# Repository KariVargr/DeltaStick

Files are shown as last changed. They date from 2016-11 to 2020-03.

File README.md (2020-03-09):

# DeltaStick
Delta Parallel Robot/Kinematics base flight stick to replace a Throttle only unit for Space Flight Sims

# Update
This project Got put on hold almost in 2018 due to Work, Life and changes in how the same it was building built for changes. i will see about Exporting Editable STL in the near future, if they are still around.

Sorry for the long delay on getting this info up and useable for everyone, i had to change a few elements to make it easier for some one to built it with out taps

Parts List Delta Body

(9) 6-32 Machine Nuts
(9) 6-32 Machine Screws 1 1/2in
(3-9) 6-32 Machine Screws 3/8in

(24) 4-40 Machine Nuts
(24) 4-40 Machine Screws Flat Head 3/4in

(9) 5/16 Machine Nuts
(3) 5/16 3in Bolt
(6) 5/16 Lock Nuts
(6) 5/15 Washer (2644)
(3) Finishing Washer
Springs

(3) 13GA 100RPM geared motor 12V (Planning on testing the 60RPM)
http://leeselectronic.com/en/product/41502.html

(3) AS5600 Hall Effect
http://www.digikey.com/product-detail/en/ams/AS5600-ASOM/AS5600-ASOMCT-ND/4914333

SMT Breakout PCB for SOIC-8
https://www.adafruit.com/product/1212

(3) 100nf capacitors
(3) 1uf capacitors

Ardunio Leonardo or Pro Micro

12V 2A DC Power Supply.

(3) TA7291SG or L298N 
You will need to find something simalure. once i have time to find a replacment this will be udpated.
(Option to Replace this with L298N Motor Driver, 2 to 3 of these will work)

(3) 10K Resistors
(3) 1k Resistors
(3) 2N3904

Wire
Prototyping PCB

(12) 608ZZ Bearings

Joystick

(6) 6-32 Machine Nuts
(6) 6-32 Machine Screws 3/4in
(9) 6-32 Machine Screws 1 1/2in

(13) Tact
(18) 10K Resistors

On-Off-On Toggle Switch

MCP23017

Thumb Joystick
https://www.sparkfun.com/products/9032

Tools

3D Printer (or Order Prints from a online site)

Small File
Sand Paper

13MM (1/2in) Wrench/Socket
14MM (9/16) Wrench/Socket

Side Cutter.

AC / Crazy Glue

Sodering Iron
Soder

wire striper with screw cutter

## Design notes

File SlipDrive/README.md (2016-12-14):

# DeltaStick Slip Drive/Axle/Rod?

(6) 608ZZ Bearings
(12) 5/16 Machine Nuts
(3) 5/16 3in Bolt / ReadyRod (Will need to be treaded all the way to the end)
(6) 5/16 Lock Nuts
(6) 5/15 Washer (2644)
(3) Finishing Washer
Springs

Parts: Each build out will need
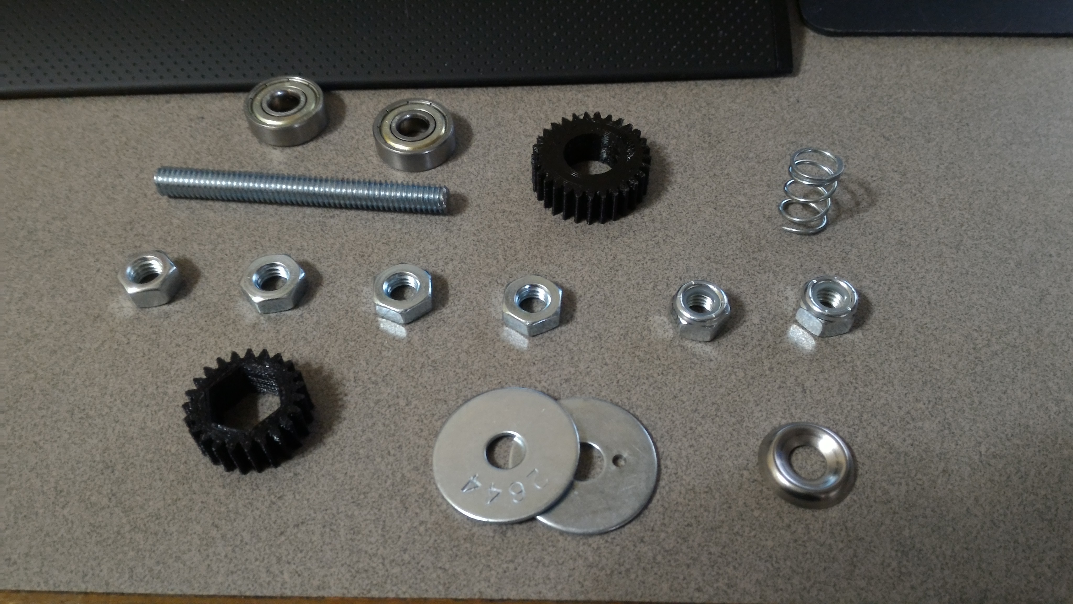
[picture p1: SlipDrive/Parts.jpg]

(2) 608ZZ Bearings
(1) 5/16 Bolt/Rod 
(4) 5/16 Machine Nuts
(2) 5/16 Lock Nuts
(2) 5/15 Washer (2644)
(1) Finishing Washer
and a Spring.

The Spring needs to fit over the 5/16 Rod with space to move, and can be cut to size but about 1in or less in length will work.

Step 1:
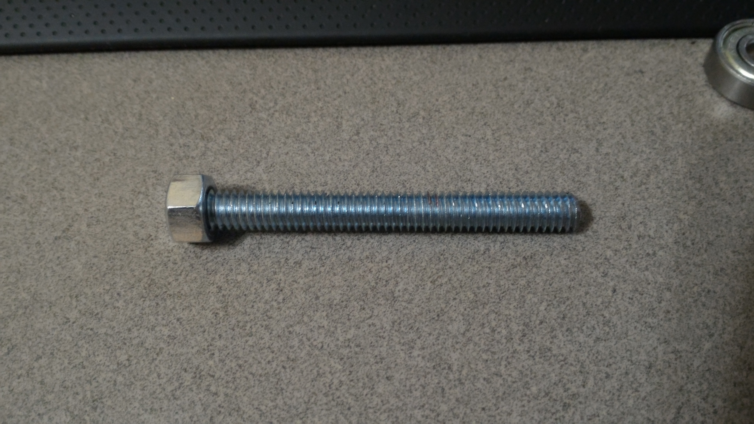
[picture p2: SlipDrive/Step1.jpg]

If you have a Bolt make sure it is threaded all they way to the end.
If you are using Ready Rod, or Threaded Rod Make sure its 3 In in length and place a 5/16 Machine Nuts at one end

Step 2:
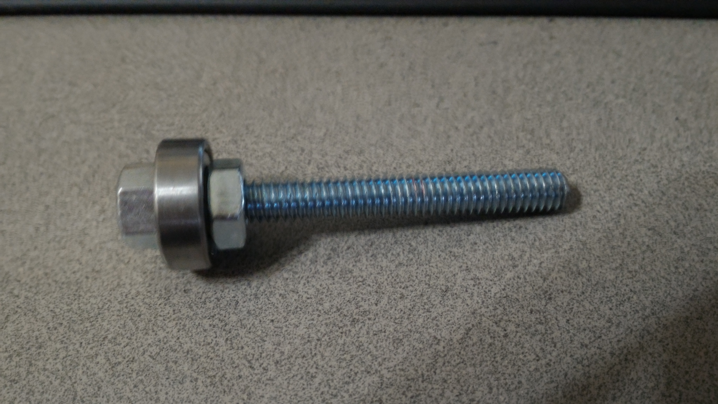
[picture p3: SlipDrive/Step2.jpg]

Slid on a 608ZZ Bearing Followed by a 5/16 Machine Nut

Step 3: 
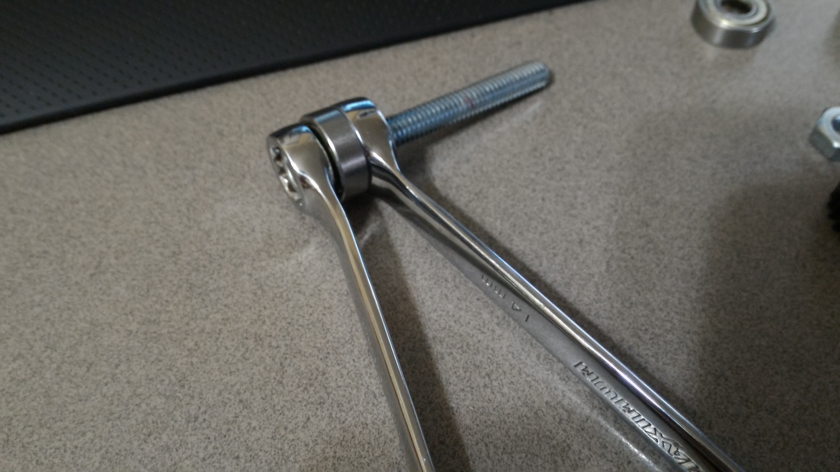
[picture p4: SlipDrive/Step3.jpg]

Tighten the 2 nuts against the bearing. the outside of the bearing should still move freely. 

Step 4: 
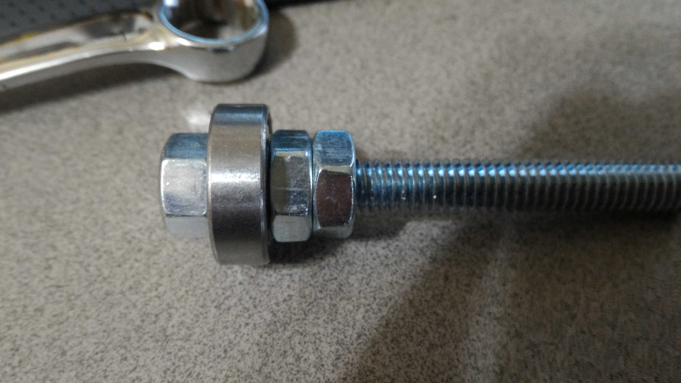
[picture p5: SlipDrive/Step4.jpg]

Place another 5/16 Machine Nut on. 

Step 5: 
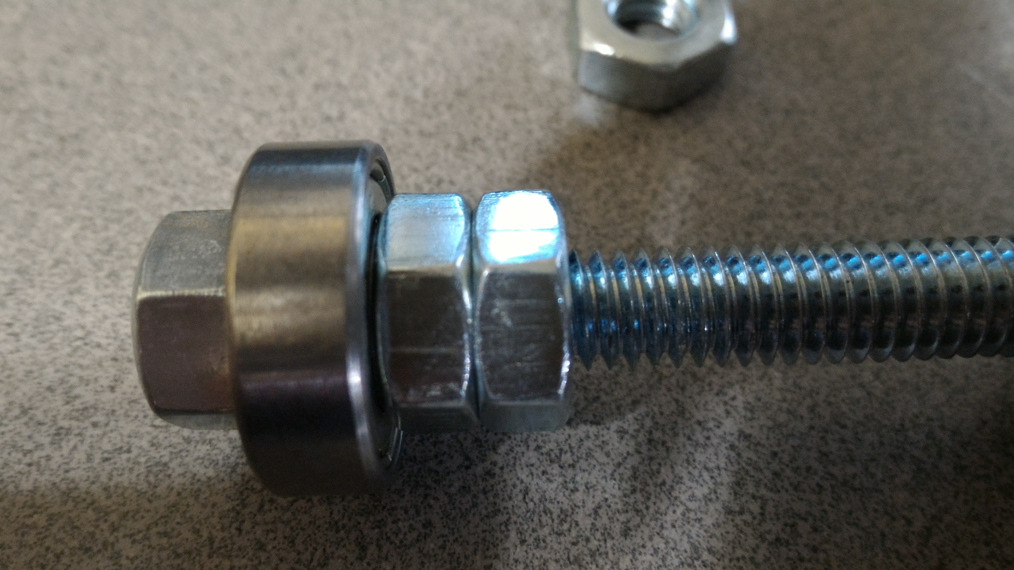
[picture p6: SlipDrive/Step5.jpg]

Tight the Nut down to the one next to it until they align in the picture.
If they cant be tightened to alignment try flipping the nut over or sanding one side of it to achieve the goal
None of the nuts should come off by hand at this point.

Step 6:
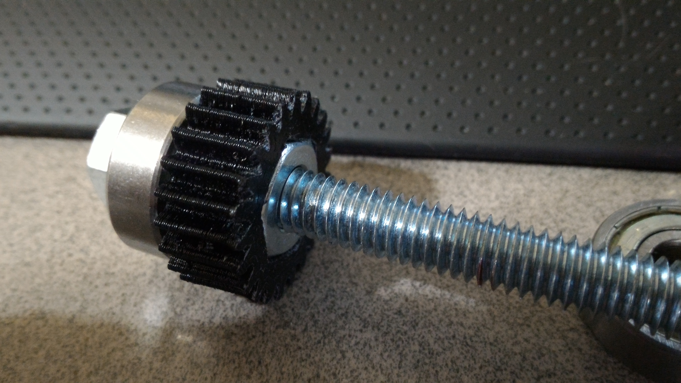
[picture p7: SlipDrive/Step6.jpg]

Slid the Printed Gear over the Machine Nuts, the gear should be centered between the nuts.

Step 7:
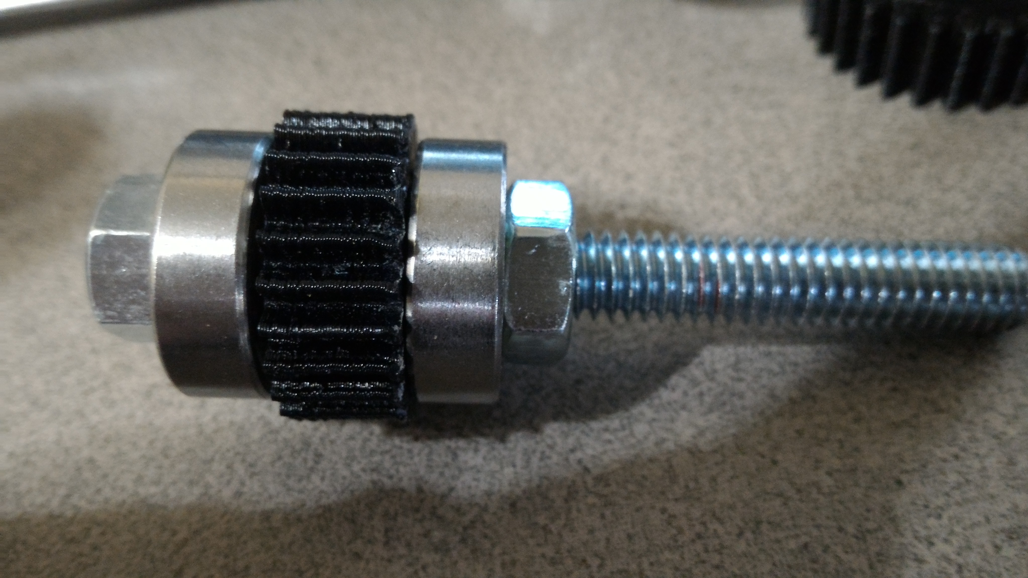
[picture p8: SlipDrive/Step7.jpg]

Slide a 2nd 608ZZ Bearing Followed by a 5/16 Machine Nut 
Tighten the nut against the bearing. the outside of the bearing should still move freely. 

No Show: At this point you would want to put the gearwall print on to the rod.

Step 8:
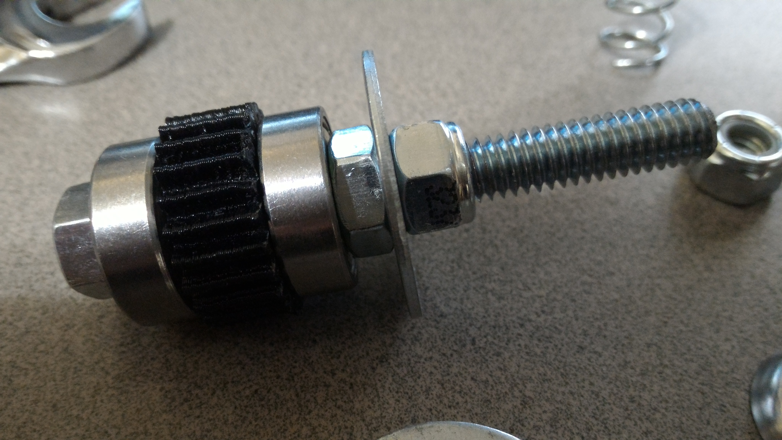
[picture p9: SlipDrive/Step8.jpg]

Slide a 5/15 Washer on followed by a 5/16 Lock Nut
Tighten the nut against the Washer.

Step 9:
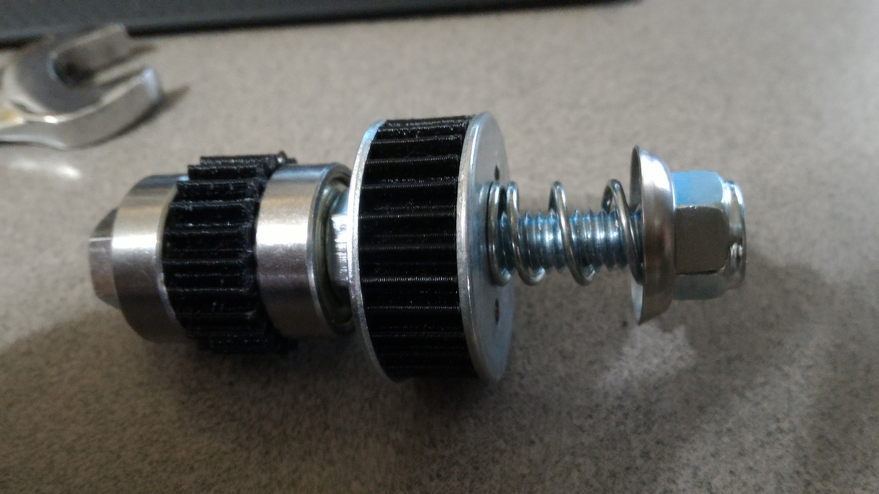
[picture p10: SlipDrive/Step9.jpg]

Place the 29T Slip Gear over the Lock Nut followed by a 5/15 Washer, Spring, Finishing Washer and Last 5/16 Lock Nut.
Tighten the nut down to a hold the stack together as in picture.

The Spring can be trimmed to allow max Slip when in the position pictured.
By Tightening the Lock Nut at the end the Friction will increase.

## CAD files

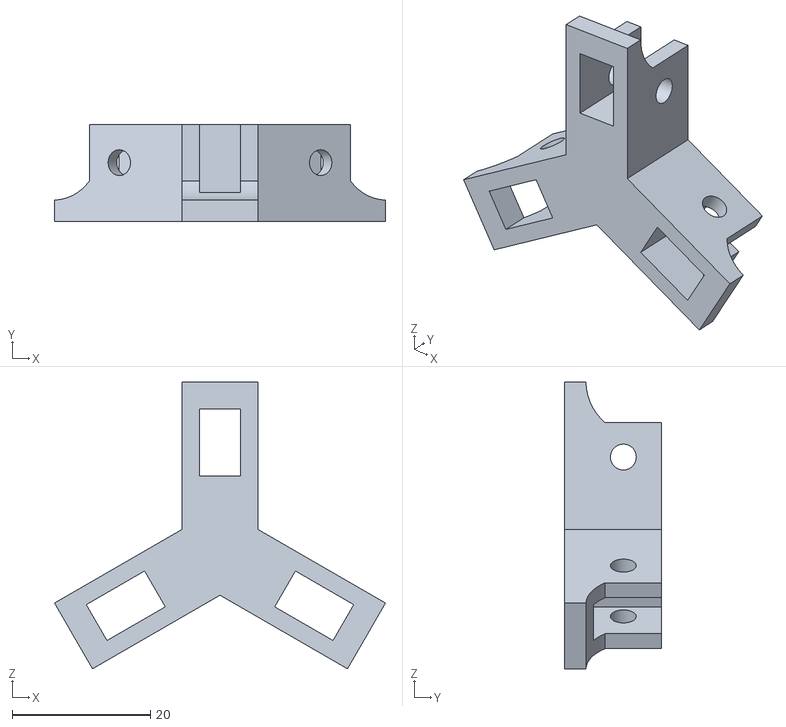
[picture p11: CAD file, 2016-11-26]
STL/CenterBot.stl
47.9 x 14.0 x 41.5

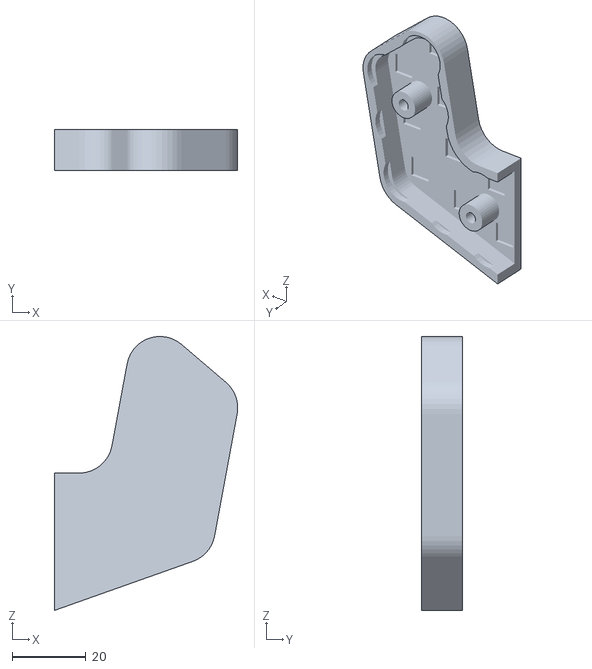
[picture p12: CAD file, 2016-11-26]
STL/JoyStick/CoverBack.STL
49.6 x 11.0 x 74.1

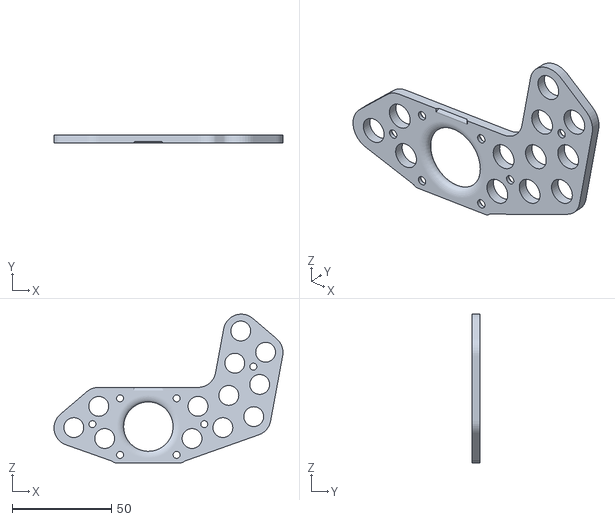
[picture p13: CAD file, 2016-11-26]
STL/JoyStick/Cover.STL
115.4 x 4.00 x 74.9

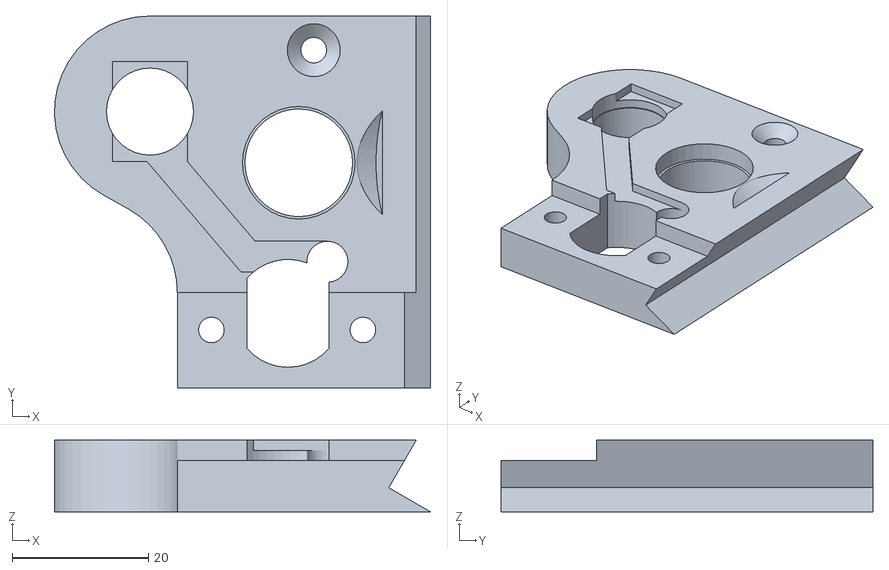
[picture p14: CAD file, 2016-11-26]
STL/MagWall.STL
55.1 x 54.5 x 10.5

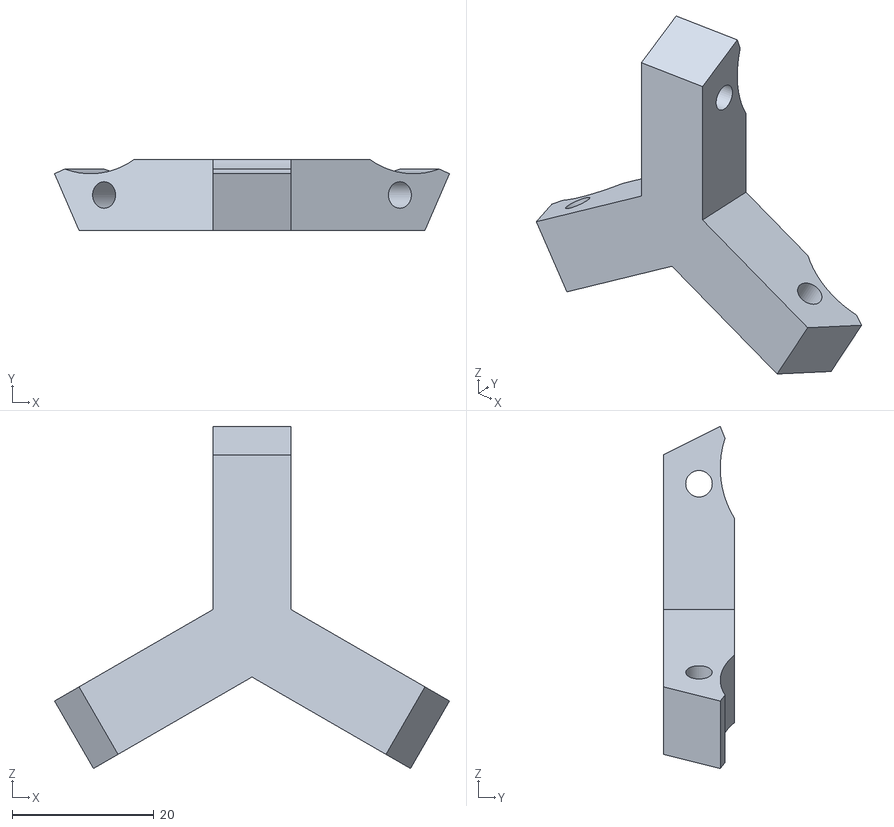
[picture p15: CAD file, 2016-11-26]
STL/CenterTop.STL
55.7 x 10.0 x 48.3

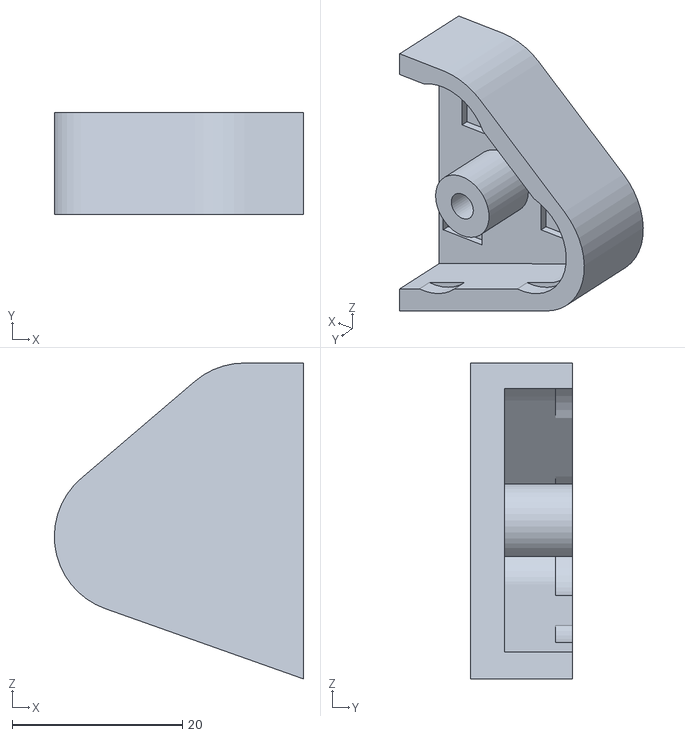
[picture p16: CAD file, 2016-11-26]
STL/JoyStick/CoverBackB.STL
29.3 x 12.0 x 37.2

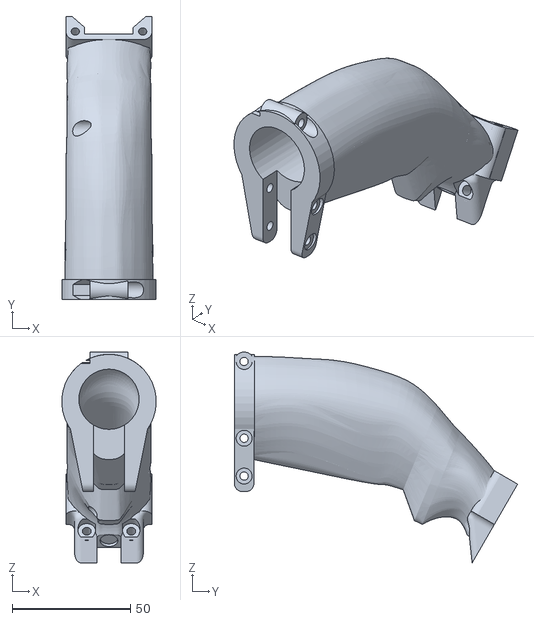
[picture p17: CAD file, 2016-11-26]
STL/JoyStick/BodyScaled.STL
39.9 x 119.9 x 89.3

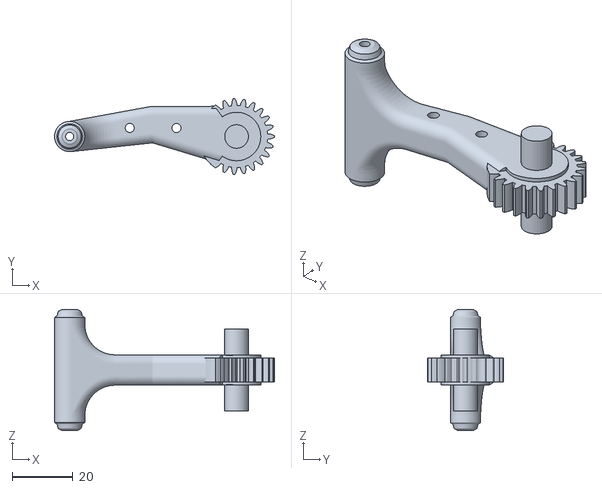
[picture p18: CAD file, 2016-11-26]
STL/LowerArmGearedCir.STL
72.5 x 25.0 x 40.0

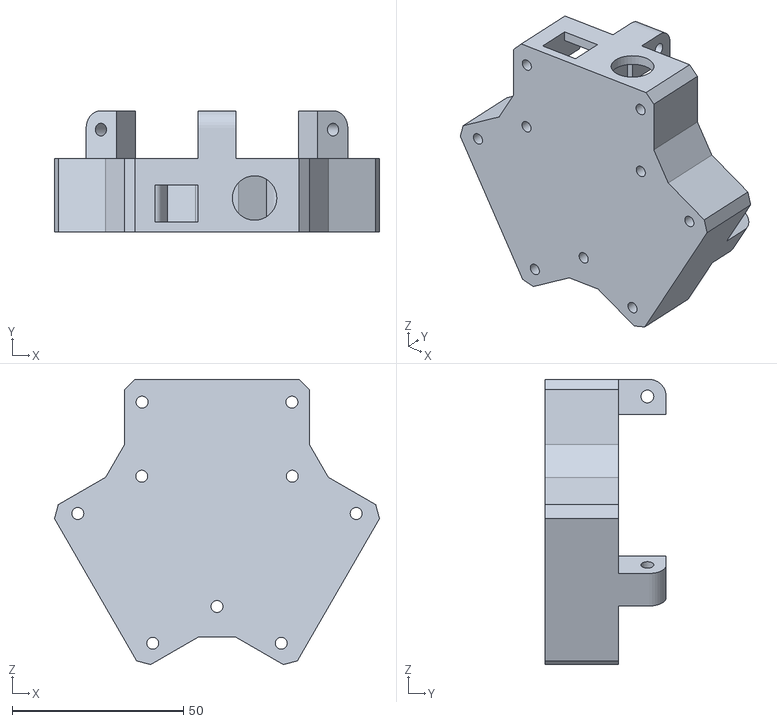
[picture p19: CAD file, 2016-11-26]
STL/ControlBox.STL
95.0 x 35.5 x 83.4

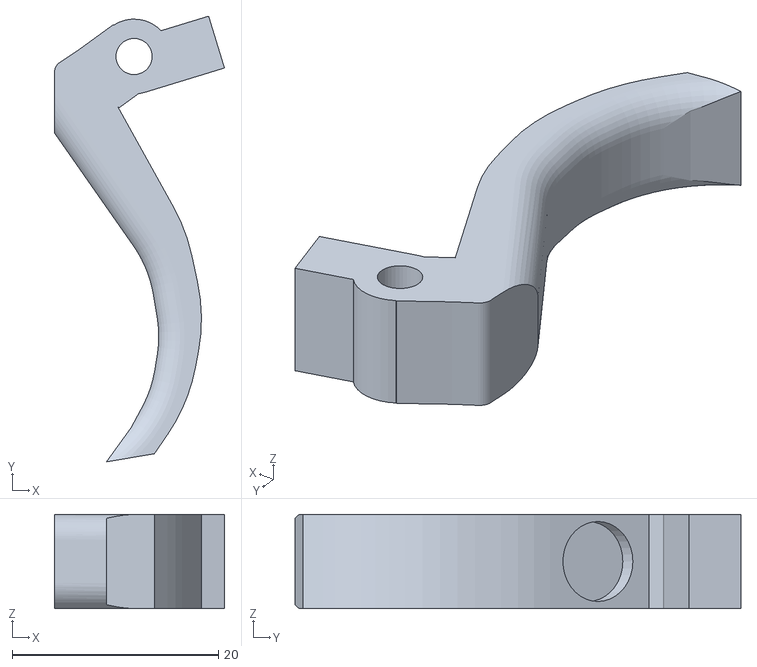
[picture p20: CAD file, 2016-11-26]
STL/JoyStick/Trigger.STL
16.5 x 43.2 x 9.12

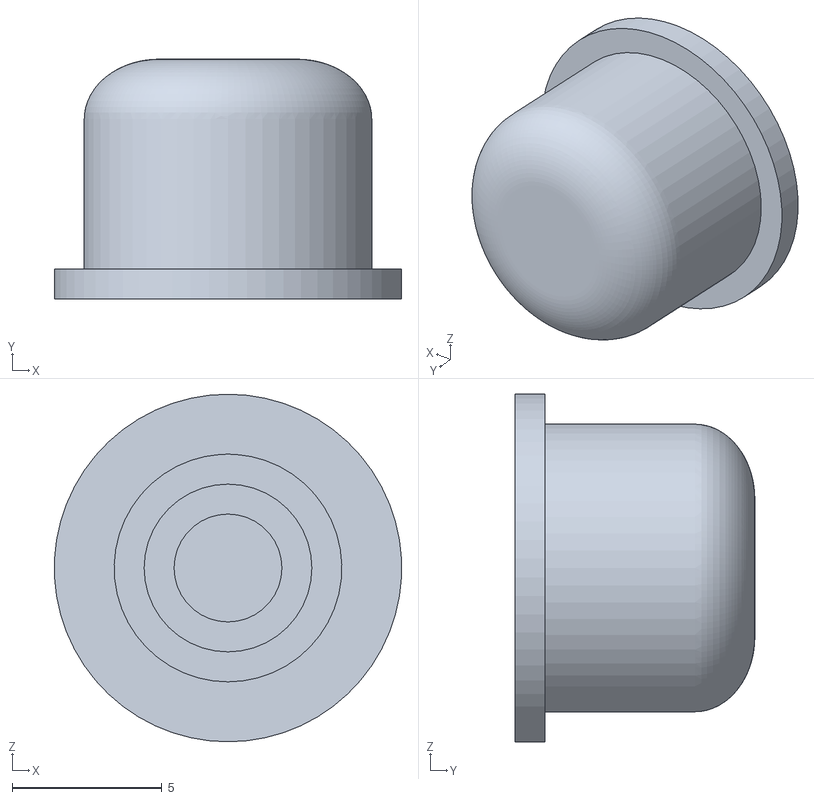
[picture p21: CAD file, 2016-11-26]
STL/JoyStick/CoverButton.STL
11.6 x 8.00 x 11.6

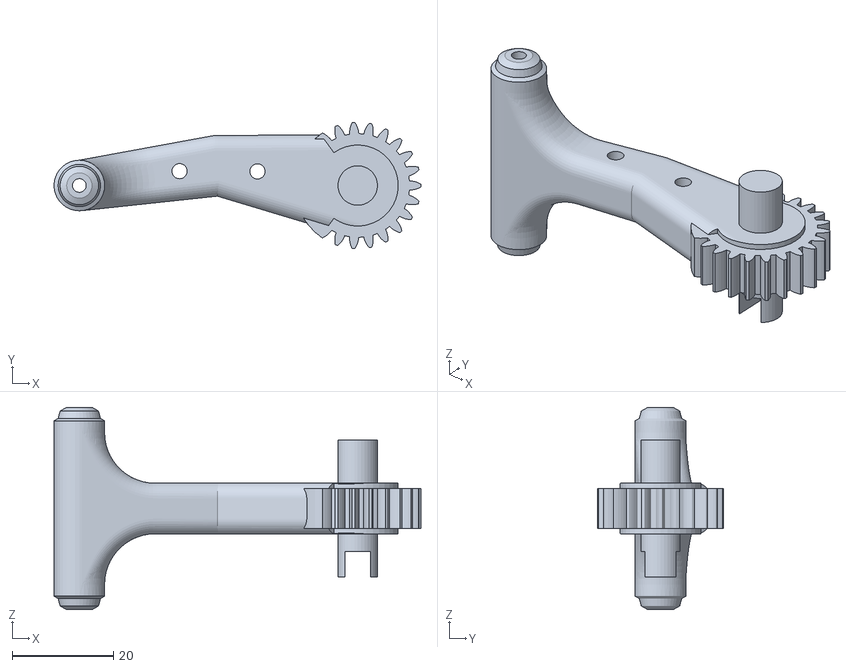
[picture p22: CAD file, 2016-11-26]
STL/LowerArmGeared.STL
72.5 x 25.0 x 40.0

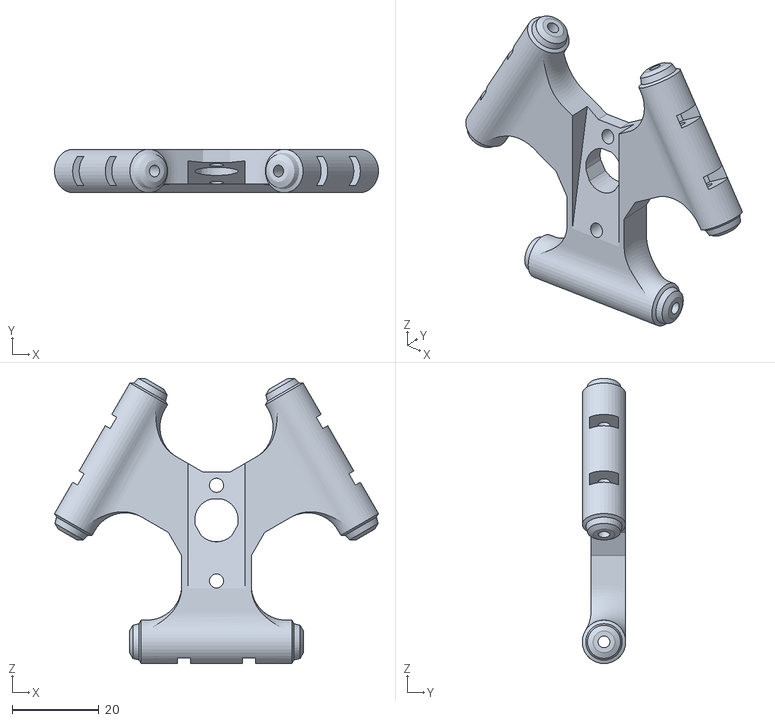
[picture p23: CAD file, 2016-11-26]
STL/Effector.STL
74.5 x 10.00 x 65.6

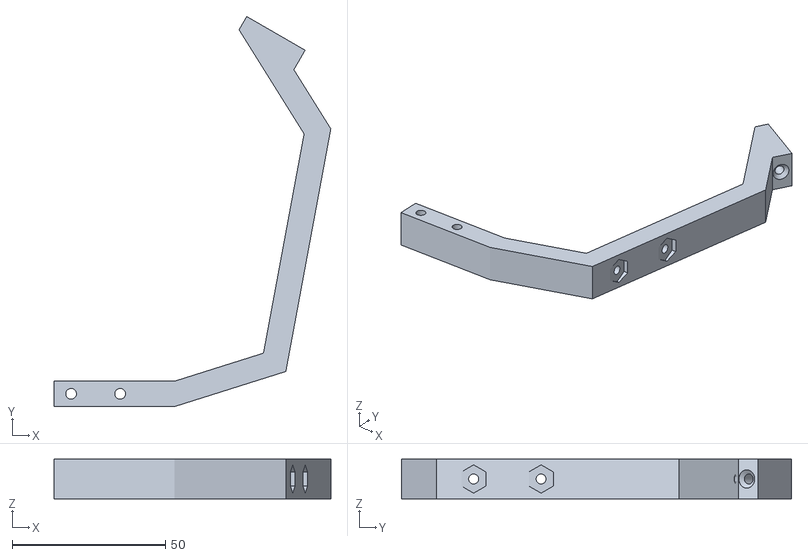
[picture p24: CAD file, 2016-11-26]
STL/JoyStick/Arc.STL
90.2 x 127.2 x 13.0

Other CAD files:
STL/15T DriveGear 3mm Shaft.STL
STL/JoyStick/HeadTall.STL
STL/29T SlipGear.STL
STL/Corner.STL
STL/23T Gear.STL
STL/ArmJoint.STL
STL/GearWall.STL
STL/ROD.STL

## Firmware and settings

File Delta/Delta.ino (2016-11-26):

#include <Adafruit_NeoPixel.h>
#include <HID-Project.h>
#include <Wire.h>
#include <SPI.h>
#include <Adafruit_MCP23017.h>
#include <math.h>
#include "DeltaCode.h"

Adafruit_MCP23017 mcp;
DELTACAL deltaCal;
Adafruit_NeoPixel strip = Adafruit_NeoPixel(0, 6, NEO_GRB + NEO_KHZ800);

float deadzone = 2.5;
float TZero = 97.00;
float Zshift = 121;

float xHome, yHome, zHome;
float xTheta, yTheta, zTheta;
float xValue, yValue, zValue;
float xT_HOME, yT_HOME, zT_HOME;

uint8_t xMaster, yMaster, zMaster;

float xMin, yMin, zMin, xMax, yMax, zMax;

int returnPower = 180;

//Setup Pins
//I2C in USE = 2, 3
//A2-A3 Free
int xTValue, yTValue;
float USBdeadzone = 10;
float xTCorrect = -10;
float yTCorrect = +42;

bool Debug = false;

int lastDEBUG = 0;
int lastUSB = 0;

int DEBUGDelay = 10;
int USBDelay = 10;

int deltaMode = 0;

int MOTORDIR[9] = {1,0, 14,15, 7,8 , 10,9,5};

void setup() {
  // put your setup code here, to run once:
  Wire.begin();
  Gamepad.begin();
  mcp.begin();
  mcp.pinMode(0, INPUT);//Thumb
  mcp.pinMode(1, INPUT);//10
  mcp.pinMode(2, INPUT);//11
  mcp.pinMode(3, INPUT);//9
  mcp.pinMode(4, INPUT);//12
  mcp.pinMode(5, INPUT);//6
  mcp.pinMode(6, INPUT);//4
  mcp.pinMode(7, INPUT);//3
  mcp.pinMode(8, INPUT);//2
  mcp.pinMode(10, INPUT);//1
  mcp.pinMode(12, INPUT);//7
  mcp.pinMode(13, INPUT);//8
  mcp.pinMode(14, INPUT);//5
  mcp.pinMode(15, INPUT);//Trigger

  pinMode(A3, INPUT); //Thumb X
  pinMode(A6, INPUT); //Thumb Y
  
  pinMode(A0, INPUT); //DELTA X
  pinMode(A1, INPUT); //DELTA Y
  pinMode(A2, INPUT); //DELTA Z

  pinMode(6, INPUT); //DELTA Modes
  pinMode(16, INPUT); //DELTA Modes

  for(int i=0; i<9; i++){
    pinMode(MOTORDIR[i], OUTPUT);
    if(i <= 5){
      digitalWrite(MOTORDIR[i], LOW);
    }else{
      analogWrite(MOTORDIR[i], returnPower);
    }
  }
  strip.begin();
  strip.show(); // Initialize all pixels to 'off'
}

void loop() {
  //DELTA MODES
    if(digitalRead(6) == 0 && digitalRead(16) == 1){
      deltaMode = 2;
    }else if(digitalRead(6) == 1 && digitalRead(16) == 0){
      deltaMode = 1;
    }else{
      deltaMode = 0;
    }
  //THUMB STICK
    xTValue = analogRead(A3)+xTCorrect;
    yTValue = analogRead(A6)+yTCorrect;
    
  //DELTA
    xTheta = round(analogRead(A0))+0;
    yTheta = round(analogRead(A1))+4;
    zTheta = round(analogRead(A2))+0;

    deltaCal.ForwardKinematic(xTheta-TZero, yTheta-TZero, zTheta-TZero, xValue, yValue, zValue);

    xMaster = map(constrain(round(xValue), -100, 100), -100, 100, 0, 255); // +- 100
    yMaster = map(constrain(round(yValue), -100, 100), -100, 100, 0, 255); // +- 100
    zMaster = map(constrain(round(zValue + Zshift), -45, 46), 46, -45, 0, 255); //-55 TOP

    //Motor Call for Centering on the XYZ HOME
    if(deltaMode == 0){
      xHome = 0;
      yHome = 0;
      zHome = 0;
    }
    if(deltaMode == 1){ //Throttle Mode
      xHome = 0;
      yHome = 0;
      zHome = zValue + Zshift;
    }
    if(deltaMode == 2){ //No Return
      xHome = xValue;
      yHome = yValue;
      zHome = zValue + Zshift;
    }

    deltaCal.InverseKinematic(xHome, yHome, zHome - Zshift, xT_HOME, yT_HOME, zT_HOME);

    DEBUG();
    checkDIR();
    submitUSB();
    delay(1);
}

void submitUSB() {
  if(lastUSB == USBDelay){
    //Delta Value USBdeadzone
    if((xMaster > 128 - USBdeadzone) && (xMaster < 128 + USBdeadzone))
    {
      xMaster = 128;
    }
    if((yMaster > 128 - USBdeadzone) && (yMaster < 128 + USBdeadzone))
    {
      yValue = 128;
    }
    if((zMaster > 128 - USBdeadzone) && (zMaster < 128 + USBdeadzone))
    {
      zMaster = 128;
    }

    //Thumb Value USBdeadzone
    if((xTValue > 512 - USBdeadzone) && (xTValue < 512 + USBdeadzone))
    {
      xTValue = 512;
    }
    if((yTValue > 512 - USBdeadzone) && (yTValue < 512 + USBdeadzone))
    {
      yTValue = 512;
    }
  
    //USB OUTPUT
      //Gamepad.press(0);
      if(mcp.digitalRead(0) == HIGH){
        Gamepad.press(14);
      }
      if(mcp.digitalRead(1) == HIGH){
        Gamepad.press(2);
      }
      if(mcp.digitalRead(2) == HIGH){
        Gamepad.press(3);
      }
      if(mcp.digitalRead(3) == HIGH){
        Gamepad.press(4);
      }
      if(mcp.digitalRead(4) == HIGH){
        Gamepad.press(1);
      }
      if(mcp.digitalRead(5) == HIGH){
        Gamepad.press(8);
      }
      if(mcp.digitalRead(6) == HIGH){
        Gamepad.press(10);
      }
      if(mcp.digitalRead(7) == HIGH){
        Gamepad.press(9);
      }
      if(mcp.digitalRead(8) == HIGH){
        Gamepad.press(12);
      }
      if(mcp.digitalRead(10) == HIGH){
        Gamepad.press(11);
      }
      if(mcp.digitalRead(12) == HIGH){
        Gamepad.press(5);
      }
      if(mcp.digitalRead(13) == HIGH){
        Gamepad.press(6);
      }
      if(mcp.digitalRead(14) == HIGH){
        Gamepad.press(7);
      }
      if(mcp.digitalRead(15) == HIGH){
        Gamepad.press(13);
      }
      
      Gamepad.xAxis(map(xMaster, 255, 0, -32765, 32765));
      Gamepad.yAxis(map(yMaster, 0, 255, -32765, 32765));
      Gamepad.rxAxis(map(zMaster, 0, 255, -32765, 32765));
      Gamepad.zAxis(map(xTValue, 0+xTCorrect, 1023+xTCorrect, -128, 127));
      Gamepad.rzAxis(map(yTValue, 0+yTCorrect, 1023+yTCorrect, -128, 127));
      Gamepad.dPad1(0);
      Gamepad.write();
      Gamepad.releaseAll();
      
    lastUSB = 0;
  }else{
    lastUSB++;
  }
}

void checkDIR() {
  if(xTheta-TZero+3 > xT_HOME + (deadzone*2)){
    digitalWrite(1, LOW);
    digitalWrite(0, HIGH);
    analogWrite(10, map(xTheta-TZero, 0, 75, 160, 80)); //180 / 105
  }else if(xTheta-TZero+3 < xT_HOME - (deadzone*2)){
    digitalWrite(1, HIGH);
    digitalWrite(0, LOW);
    analogWrite(10, map(xTheta-TZero, 0, -66, 160, 80));
  }else{
    digitalWrite(1, LOW);
    digitalWrite(0, LOW);
  }
  
  if(yTheta-TZero > yT_HOME + deadzone){
    digitalWrite(14, LOW);
    digitalWrite(15, HIGH);
    analogWrite(9, map(yTheta-TZero, 0, 75, 160, 80));
  }else if(yTheta-TZero < yT_HOME - deadzone){
    digitalWrite(14, HIGH);
    digitalWrite(15, LOW);
    analogWrite(9, map(yTheta-TZero, 0, -66, 160, 80)); 
  }else{
    digitalWrite(14, LOW);
    digitalWrite(15, LOW);
  }

  //analogWrite(6, returnPower);
  if(zTheta-TZero > zT_HOME + deadzone){
    digitalWrite(7, LOW);
    digitalWrite(8, HIGH);
    analogWrite(5, map(zTheta-TZero, 0, 75, 160, 80));
  }else if(zTheta-TZero < zT_HOME - deadzone){
    digitalWrite(7, HIGH);
    digitalWrite(8, LOW);
    analogWrite(5, map(zTheta-TZero, 0, -66, 160, 80));
  }else{
    digitalWrite(7, LOW);
    digitalWrite(8, LOW);
  }
}

void DEBUG () {
  if(lastDEBUG == DEBUGDelay && Debug == true){
    Serial.print("deltaMode: ");
    Serial.println(deltaMode);
    Serial.println("MASTER - RAW - DELTA - RETURN - MIN - MAX - POWER: ");
    Serial.print("X: ");
    Serial.print(xMaster);
    Serial.print(" - ");
    Serial.print(xTheta);
    Serial.print(" - ");
    Serial.print(xValue);
    Serial.print(" - ");
    Serial.print(xT_HOME + TZero);
    Serial.print(" - ");
    Serial.print(xMin);
    Serial.print(" - ");
    Serial.println(xMax);
    Serial.print("Y: ");
    Serial.print(yMaster);
    Serial.print(" - ");
    Serial.print(yTheta);
    Serial.print(" - ");
    Serial.print(yValue);
    Serial.print(" - ");
    Serial.print(yT_HOME + TZero);
    Serial.print(" - ");
    Serial.print(yMin);
    Serial.print(" - ");
    Serial.println(yMax);
    Serial.print("Z: ");
    Serial.print(zMaster);
    Serial.print(" - ");
    Serial.print(zTheta);
    Serial.print(" - ");
    Serial.print(zValue + Zshift);
    Serial.print(" - ");
    Serial.print(zT_HOME + TZero);
    Serial.print(" - ");
    Serial.print(zMin);
    Serial.print(" - ");
    Serial.println(zMax);

    if(xValue < xMin){ xMin = xValue; }
    if(yValue < yMin){ yMin = yValue; }
    if(zValue + Zshift < zMin){ zMin = zValue + Zshift; }

    if(xValue > xMax){ xMax = xValue; }
    if(yValue > yMax){ yMax = yValue; }
    if(zValue + Zshift > zMax){ zMax = zValue + Zshift; }
    
    lastDEBUG = 0;
  }else{
    lastDEBUG++;
  }
}
